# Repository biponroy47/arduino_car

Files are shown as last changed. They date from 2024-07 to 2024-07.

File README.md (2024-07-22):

## Notes

#### 1st Update
My initial idea was to replicate the functionality of an actual RWD car, where the front wheels are designated for steering, and the rear wheels are for forward/reverse movement. Implementing the motors for forward/reverse movement is simple but steering was a bit of an issue. My idea was to use 2 servo motors attached to their respective axles and wheels to implement this, but I only had 1 servo motor at the moment. 

My next solution for this problem was to use the single servo motor and attach it to a singular longer axle with both wheels attached to the sides,  but once again I did not have a simple T-shaped shaft to attach to the 21-spline gear-shaped tip of the servo.

I then thought of printing my own connector. I found a 3D model of the 21-spline tip online and attempted to print a custom model for this shaft. The model was functional in theory, however the 3D printer was unable to print such precise details of the spline, it ended up fusing together to create a small cylindrical tube instead. 

At this point I had given up on the idea for separate steering. I could always print out some arms, buy some bearings, some screws, attach all the arms together with the servo to achieve this, but simplicity was my priority here as I have a bad habit of uncessessarily overcomplicating things. 
#### 2nd Update
Anyways, here I decided to go back to my original plan, the standard 4 wheel design where each wheel can only move forwards or backwards, and rotation can be achieving by alternating the direction of the linearly grouped motors. Personally, I'm not a fan of this design but it'll have to do.

So now I've begun laying out the schematic for the circuit on TinkerCAD. I was hoping to control the vehicle wirelessly, but my only options were an analog joystick which must be wired, or this IR Remote/receiver pair. I chose the IR Remote, and while everything is functional at the moment, there is one issue. The issue is that the IR Remote does not transmit a signal once an input is released, therefore my car will continue moving in the last inputted direction without ever coming to a stop. 

Simple solution would be to add a few buttons to control speed of the car, or a brake, or I could code a timeout function that would automatically bring the car to a rolling stop if an input hasn't been clicked in a while. For the sake of simplicity, I decided to set one of the buttons as a break. 
#### 3rd Update
So now I've got the prototype layed out on the UNO and it appears there are a few issues. First issue is that it appears the Arduino isn't receiving enough power via the 5v Vin pin. I've remedied this using a separate 9v battery to power the arduino separately which I will attach to the same switch in the near future.

The second issue is that the 4th motor is not working. I've implemented a simple program to run all the motors once the switch is enabled, this lost one remains stationary. I imagine this to be due to a poor soldering connection to the motor terminals, or misplaced/loose jumper cables. 

The final and main issue is the IR sensor/remote not working. I suspect it is due to the code being from a newer library which I will likely have to downgrade to the older IR Remote 2.0 library.
#### 4th Update
After inspecting the motor, I was correct and the motor was faulty. I removed it, testing it with it's own isolated battery, different jumper cables, and resoldered connections, but it did not work. Luckily I did have a couple spares to replace it with.

For the IR Remote issue, I downgraded the library and reverted the code to the older syntax. At this point the IR sensor was still not working. It turns out 2 jumper cables were swapped, specifically the power cable, and output cable. Now the LED onboard the sensor lit up indicating it received power, however the sensor still did not work.

After further research, I realized that the sensor was not compatible with an analog pin. I had run out of digital PWM pins. I realized 1 of the cables did not need PWM so after some reconfigration, the IR sensor outpput was connected to a digital output PWM pin, and the sensor finally began receiving codes from the remote.
#### Final Update
Now everything is connected properly and the prototype is complete. All motors were functional, the remote was mapped and we were ready to begin testing. Upon testing, I noticed a few things. The first thing I noticed was that the sensor would not always respond right away, I would have to click multiple times. This could not be remedied and I would just have to use a different wireless communication method for the future.

The second thing I noticed was that the car would sometimes crash after it was signalled to stop. This was due to the momentum of the motors that remained even after losing power. The car would only come to a rolling stop. I remedied this by inputting the oposite direction for a split second, then signalled it to stop. I could code it to automatically do this everytime the brake was clicked, but I couldn't be bothered.
## Future Design Improvements
- Use pre-built RC transmitter or create a custom controller with analog joysticks, arduino nano, and RF transmitted/receiver modules for wireless comunication (more accurate and responsive than IR remote/receiver)
- Separate steering by using 1 servo motor, and rack and pinion steering system (more control over movement, precise turning, but may be difficult to model/coordinate componenents)
- Create custom chasis for drive train using appropriate gear ratios for optimized torque/speed, and only utilizes 1 motor (reduces number of motors, power consumption, more efficient)
- Solder all components using perfboard/veroboard/strip board (reduces wires, space, and improves organization)
## Lessons Learned 
- Put more focus into circuit planning and pre-testing
- Model entire build before building prototype (component by component)
- Incorporate screws, nuts, bolts, and bearings into 3D model
- Animate the assembly before 3D printing
- Once 3D model and circuit is sound, then and only then buy the necessary parts needed to build the prototype
#### Final Remark
I think the main flaw with my process was trying to force the parts I had to be used in the project. Before starting the project, I bought a simple Arduino kit and a  DC motor kit. The latter kit had wheels, axles, gears, and an assortment of other parts. Now what I should've done here is modelled those parts (the ones to be used) and incorporated them into a master 3D model. Instead I went on ahead glueing parts together, attaching things, soldering wires, 3D printing stuff, and I did all this before planning how it should all work together. This caused more problems expected and things became complicated quite quickly. Had I planned better and bought/used parts according to the model instead, this project would have gone much smoother. 

The main lesson I learned here is to <b>PLAN EVERYTHING</b>. Do not rush and buy parts for the sake of having it available. Don't force parts or assemble them into your project before planning how they will work. <b>PLAN EVERYTHING!</b> 

Anyways, here are some photos of the prototype if you're curious :)

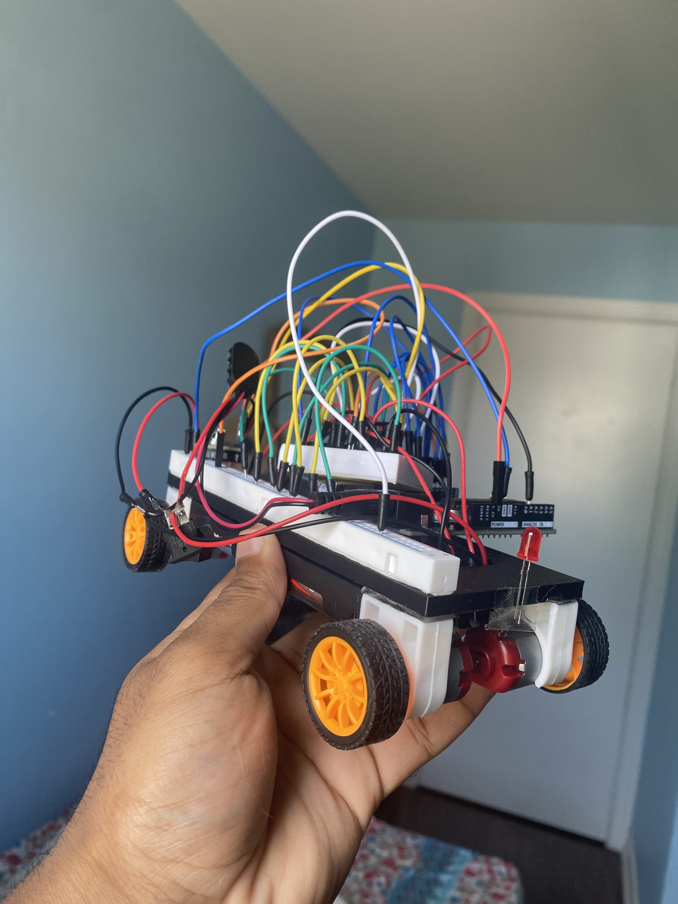
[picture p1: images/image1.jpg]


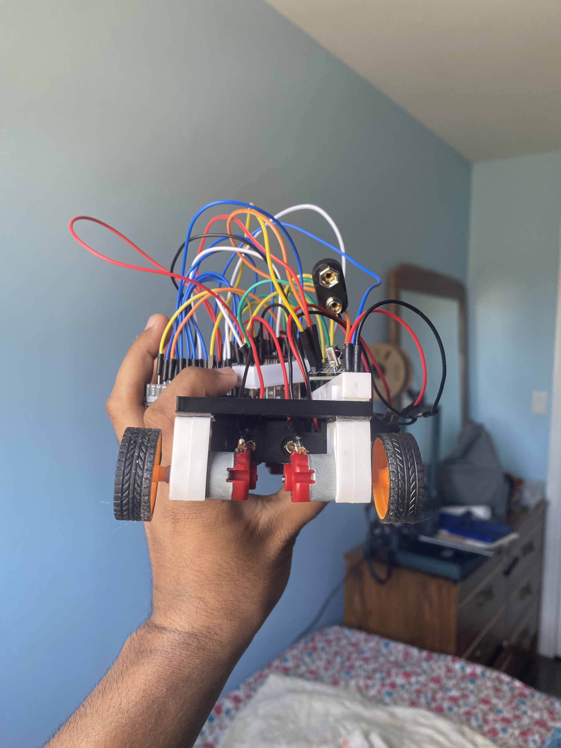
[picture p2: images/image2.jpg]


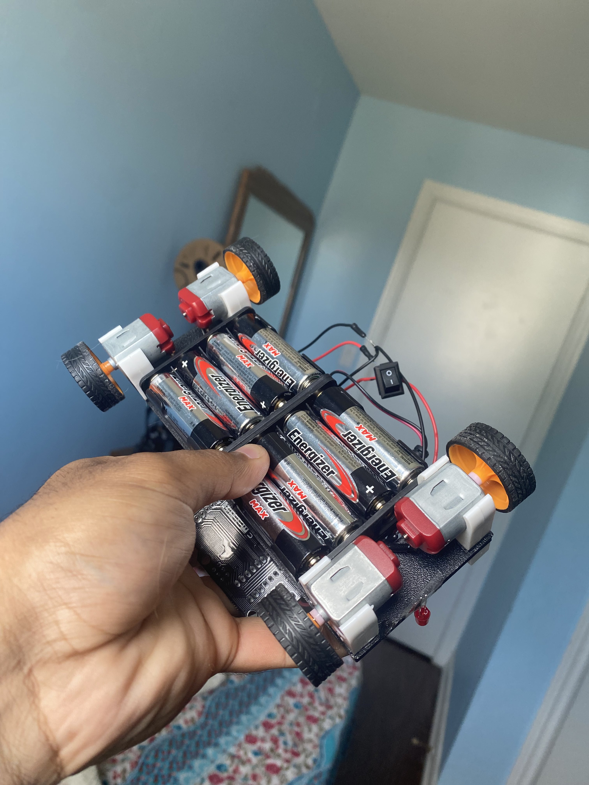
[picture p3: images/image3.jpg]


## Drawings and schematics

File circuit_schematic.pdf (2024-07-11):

A

1 | 2 | 3 | 4 | 5 | 6

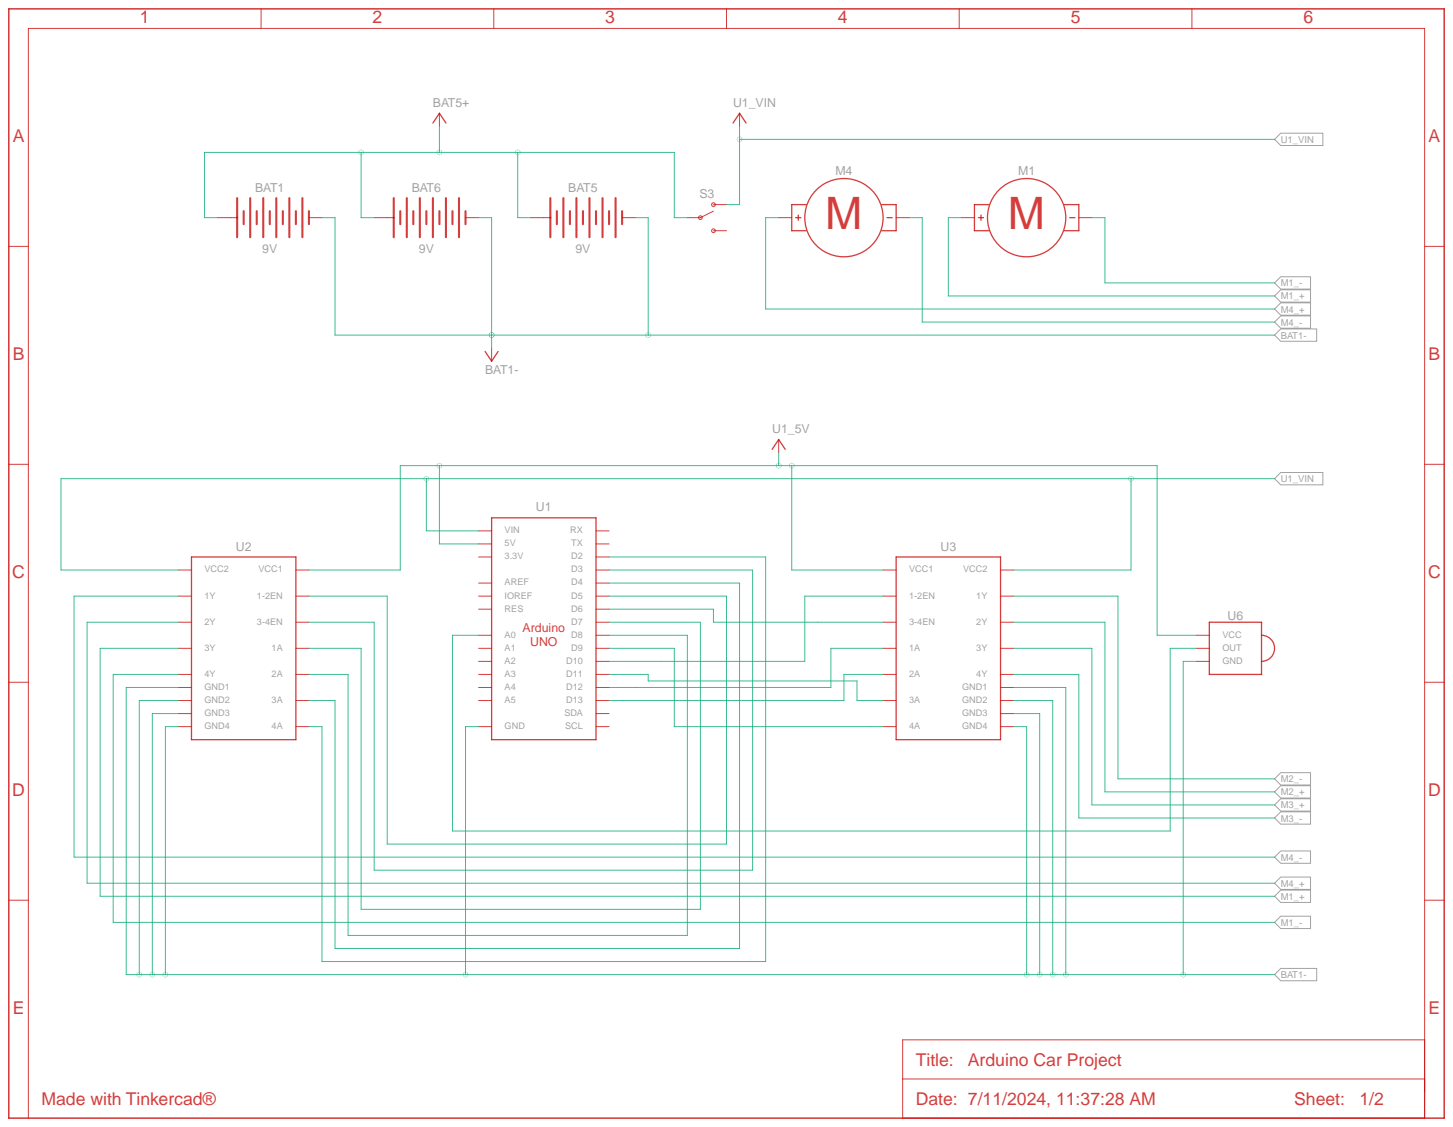
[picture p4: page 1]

Title: Arduino Car Project

A

1 | 2 | 3 | 4 | 5 | 6

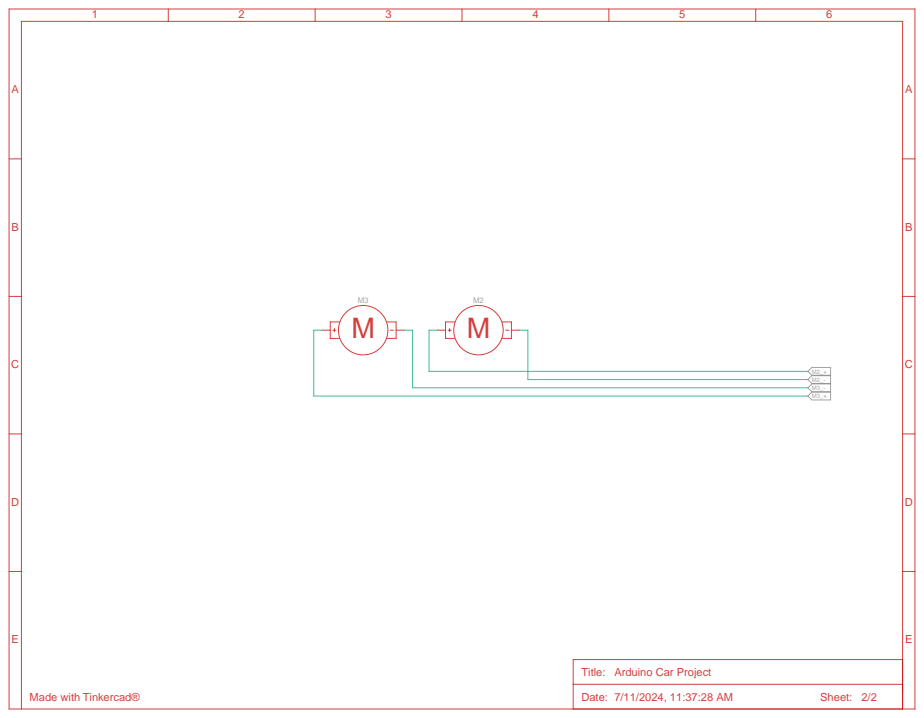
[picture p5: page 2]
Date: 7/11/2024, 11:37:28 AM; Sheet: 2/2

Title: Arduino Car Project

Made with Tinkercad®

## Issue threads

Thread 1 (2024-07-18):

Separate power for Vcc1 and Vcc2

biponroy47, 2024-07-18:
Disconnect Vcc1 on both chips from 12v, replace with Arduino 5v out.

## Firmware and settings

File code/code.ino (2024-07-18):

#include <IRremote.h>
int IR_RECEIVE_PIN = 11;
IRrecv irrecv(IR_RECEIVE_PIN);

int m1 = 3;
int m1a = 4;
int m1b = 2;

int m2 = 6;
int m2a = A1;
int m2b = 9;

int m3 = 5;
int m3a = 8;
int m3b = 7;

int m4 = 10;
int m4a = 13;
int m4b = 12;

void setup() {
  Serial.begin(9600);
  irrecv.enableIRIn();
  pinMode(m1, OUTPUT);
  pinMode(m1a, OUTPUT);
  pinMode(m1b, OUTPUT);
  pinMode(m2, OUTPUT);
  pinMode(m2a, OUTPUT);
  pinMode(m2b, OUTPUT);
  pinMode(m3, OUTPUT);
  pinMode(m3a, OUTPUT);
  pinMode(m3b, OUTPUT);
  pinMode(m4, OUTPUT);
  pinMode(m4a, OUTPUT);
  pinMode(m4b, OUTPUT);
}

void loop() {
  if (irrecv.decode()) {
    //UP
    if (irrecv.decodedIRData.decodedRawData == 3108437760) {
      Serial.print("FORWARD");
      digitalWrite(m1, HIGH);
      digitalWrite(m1a, LOW);
      digitalWrite(m1b, HIGH);
      digitalWrite(m2, HIGH);
      digitalWrite(m2a, HIGH);
      digitalWrite(m2b, LOW);
      digitalWrite(m3, HIGH);
      digitalWrite(m3a, LOW);
      digitalWrite(m3b, HIGH);
      digitalWrite(m4, HIGH);
      digitalWrite(m4a, HIGH);
      digitalWrite(m4b, LOW);
    } 
    //LEFT
    else if (irrecv.decodedIRData.decodedRawData == 3141861120) {
      Serial.print("LEFT");
      digitalWrite(m1, HIGH);
      digitalWrite(m1a, HIGH);
      digitalWrite(m1b, LOW);
      digitalWrite(m2, HIGH);
      digitalWrite(m2a, HIGH);
      digitalWrite(m2b, LOW);
      digitalWrite(m3, HIGH);
      digitalWrite(m3a, HIGH);
      digitalWrite(m3b, LOW);
      digitalWrite(m4, HIGH);
      digitalWrite(m4a, HIGH);
      digitalWrite(m4b, LOW);
    } 
    //RIGHT
    else if (irrecv.decodedIRData.decodedRawData == 3158572800) {
      Serial.print("RIGHT");
      digitalWrite(m1, HIGH);
      digitalWrite(m1a, LOW);
      digitalWrite(m1b, HIGH);
      digitalWrite(m2, HIGH);
      digitalWrite(m2a, LOW);
      digitalWrite(m2b, HIGH);
      digitalWrite(m3, HIGH);
      digitalWrite(m3a, LOW);
      digitalWrite(m3b, HIGH);
      digitalWrite(m4, HIGH);
      digitalWrite(m4a, LOW);
      digitalWrite(m4b, HIGH);
    } 
    //DOWN
    else if (irrecv.decodedIRData.decodedRawData == 3927310080) {
      Serial.print("FORWARD");
      digitalWrite(m1, HIGH);
      digitalWrite(m1a, HIGH);
      digitalWrite(m1b, LOW);
      digitalWrite(m2, HIGH);
      digitalWrite(m2a, LOW);
      digitalWrite(m2b, HIGH);
      digitalWrite(m3, HIGH);
      digitalWrite(m3a, HIGH);
      digitalWrite(m3b, LOW);
      digitalWrite(m4, HIGH);
      digitalWrite(m4a, LOW);
      digitalWrite(m4b, HIGH);
    } 
    //MIDDLE
    else if (irrecv.decodedIRData.decodedRawData == 3208707840) {
      Serial.println("STOP");
      digitalWrite(m1, LOW);
      digitalWrite(m2, LOW);
      digitalWrite(m3, LOW);
      digitalWrite(m4, LOW);
    }
    else {
      Serial.println(irrecv.decodedIRData.decodedRawData);
    }
    delay(200);
  }
  irrecv.resume();
}
